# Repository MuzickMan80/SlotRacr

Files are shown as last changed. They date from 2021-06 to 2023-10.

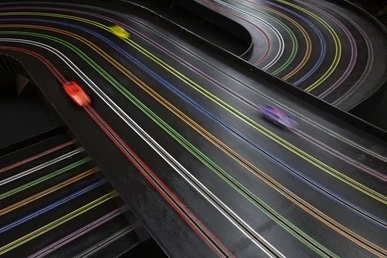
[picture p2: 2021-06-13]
frontend/assets/background.bmp

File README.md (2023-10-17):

Materials:
1 x HDMI Cable ($6) [https://www.adafruit.com/product/2775]
1 x Raspberry Pi 3 A+ ($25) [https://www.adafruit.com/product/4027]
1 x 5v 2.5a supply ($8) [https://www.adafruit.com/product/1995]
1 x 8GB SD Card
8 x Photo Transistor ($4) [https://www.adafruit.com/product/2831]
8 x 5.6kohm Resistor ($1)
8 x 1kohm Resistor ($1)

F to M jumper wires ($2) [https://www.adafruit.com/product/1954]
1 x Breadboard ($5) [https://www.adafruit.com/product/64]

1 x HDMI Display ($42) [https://www.amazon.com/Yasoca-Inch-Monitor-HDMI-Raspberry/dp/B089YSHMYS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]
Total: $93

Raspberry Pi setup:
1. Using Belena Etcher, burn Raspbian Lite OS image to the SD Card
1. Connect keyboard and monitor to Raspberry Pi, and let it startup
1. Login using username 'pi' and password 'raspberry'
1. Run 'sudo raspi-config' to enable WiFi and login to your network
  1. Select System Options->Wireless LAN and enter your SSID and password
  1. Select Interface Options->SSH to enable SSH access to your Raspberry Pi
1. Restart the Raspberry Pi to let it connect to your network
1. Run 
1. After it reboots, login again, and type the 'ifconfig' command to get the IP address for your network

From your computer:
1. Copy files to Raspbery Pi `./deploy.sh <pi ip>`

## References
https://disconnected.systems/blog/custom-rpi-image-with-github-travis/#travis
https://medium.com/platformer-blog/creating-a-custom-raspbian-os-image-for-production-3fcb43ff3630

## Ideas
Stop oog timer when red
Min 3 laps notice of low gas
Save race results
Online results database
Local sounds when low on gas

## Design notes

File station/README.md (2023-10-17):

# BOM Per Station
* $35 - Le Potato [https://www.amazon.com/dp/B0BDR2LWPC]
* $4  - 32gb microSD [https://www.amazon.com/dp/B07V1WC64X]
* $6  - USB Speaker [https://www.aliexpress.us/item/3256805016438808.html]
* $3  - USB Power Breakout [https://www.amazon.com/dp/B09W2QHL2P]
* $10 - RFID Card Reader [https://www.amazon.com/dp/B0B4BJK3W2]
* $3  - Ethernet Patch Cable [https://www.amazon.com/dp/B003EDZEDI]

Total Per Station: $61

# BOM Per Track
* $45 - 16 ports unmanaged switch 2x[https://www.amazon.com/dp/B07PFYM5MZ]
* $3  - Ethernet Patch Cable [https://www.amazon.com/dp/B003EDZEDI]
* $13 - USB Ethernet Adapter [https://www.amazon.com/dp/B00YUU3KC6]
* $10 - 30 Pack RFID Cards [https://www.amazon.com/gp/product/B07P8NCX55]

Total Per Track: $71
Total for 8 statsions: $498

# Le Potato Setup
1. Use Raspberry Pi Imager to burn Raspbian 11 lite to microSD cards [https://distro.libre.computer/ci/raspbian/11/2023-05-03-raspbian-bullseye-arm64%2Baml-s905x-cc.img.xz]
2. Enable SSH by creating empty file in boot partition called `ssh`
3. Set initial username and password by creating file called `userconf` containing username:encryptedpassword.  You can get the encrypted password via the command `openssl passwd -6`
4. Enable connection sharing to your Ethernet port on your development PC
5. Insert the microSD card into the Le Potato, connect an ethernet cable to your development PC, and power up the board.
6. Find the IP address of your Le Potato after it boots (this will take a little time, look for the green light to come on)
7. SSH into your Le Potato
8. Enable sound using `alsamixer`
  * Set volume (ACODEC) to 80
  * Set AIU ACODEC OUT EN to ON (Press M key)
  * Set AIU ACODEC SRC to I2S
9. Execute `sudo alsactl store` to persist settings

# Resources
[https://www.raspberrypi.com/documentation/computers/remote-access.html#setting-up-an-ssh-server]

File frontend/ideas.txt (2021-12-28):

Names (3 letters)
Seconds behind leader
Race Length
Save race data (for later replay)

Last Lap - White Flag

Final Lap - Checkerboard
  After finisher, everyone can finish last Lap

Flag if a racer is "missing"

New Leader

Race Report - 

Speaker - 
  When someone passes the leader
  When someone is gaining on the leader (over 5 laps)
  10 laps to go

Track disabling relays
Track slowing relays
Lane slowing relays
  Slow just one Lane

40 ohms on 13v ~ 6v  200mA @ 6v

12VA 600mA

Pit button
  When you push it, slows the Track
  If you push it too late, penalized
  When pass finish line, track shuts off
  If come in speeding, lose a Lap
  If speeding out of the pits, stop and go
  Lloyd Ruby 

Press Once to indicate they are going to pits
  Hold down at least 1.5 seconds before crossing finish line, slow 
  1.0 seconds - guaranteed speeding penalty

Need to tap within 2 seconds of crossing
  Resets after crossing finish

Status -
  Coming into pit = flashing yellow
  Slowing into pit = yellow
  Penalty = blue?
    Stop and go
  
Want 50, 100, 200 lap races
Typical race is 200 laps
  need to refuel every 45-48 laps

Time Trials mode - show current racer on top

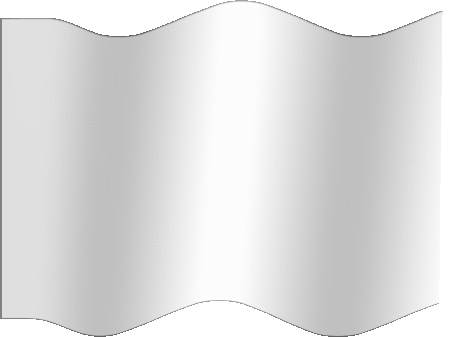
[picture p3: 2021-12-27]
frontend/assets/white-flag.gif

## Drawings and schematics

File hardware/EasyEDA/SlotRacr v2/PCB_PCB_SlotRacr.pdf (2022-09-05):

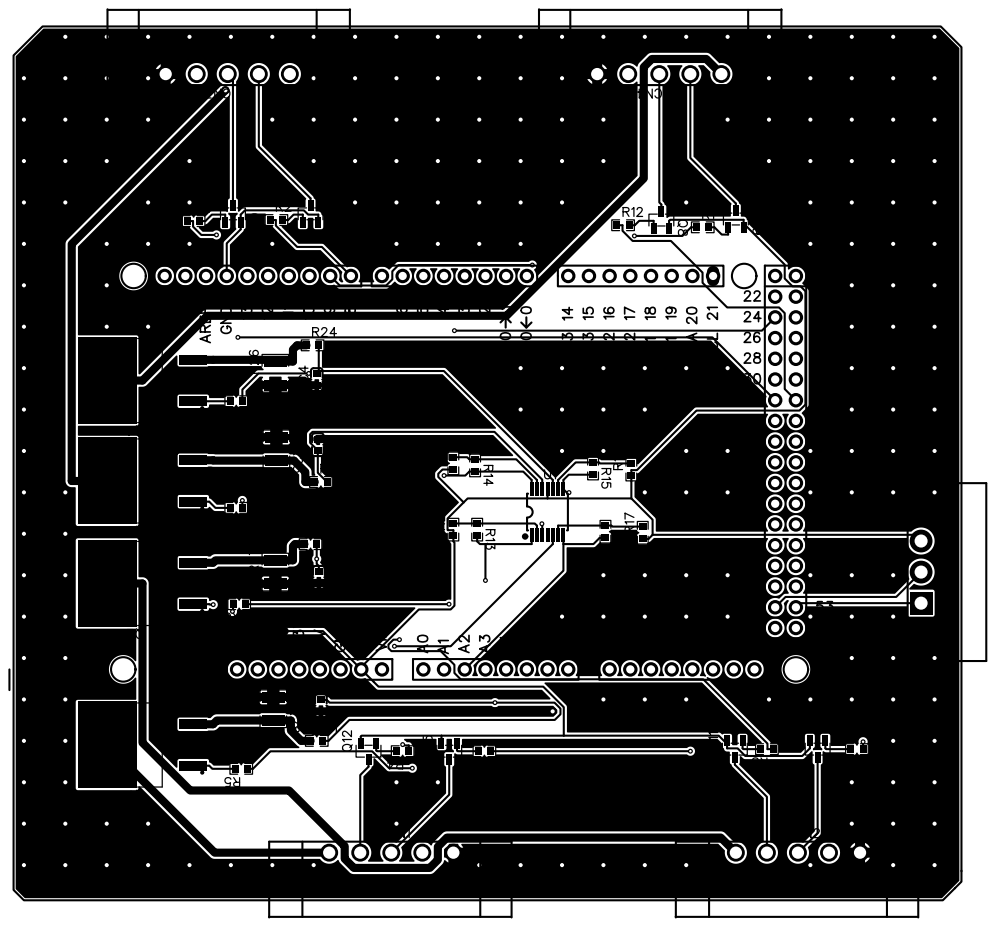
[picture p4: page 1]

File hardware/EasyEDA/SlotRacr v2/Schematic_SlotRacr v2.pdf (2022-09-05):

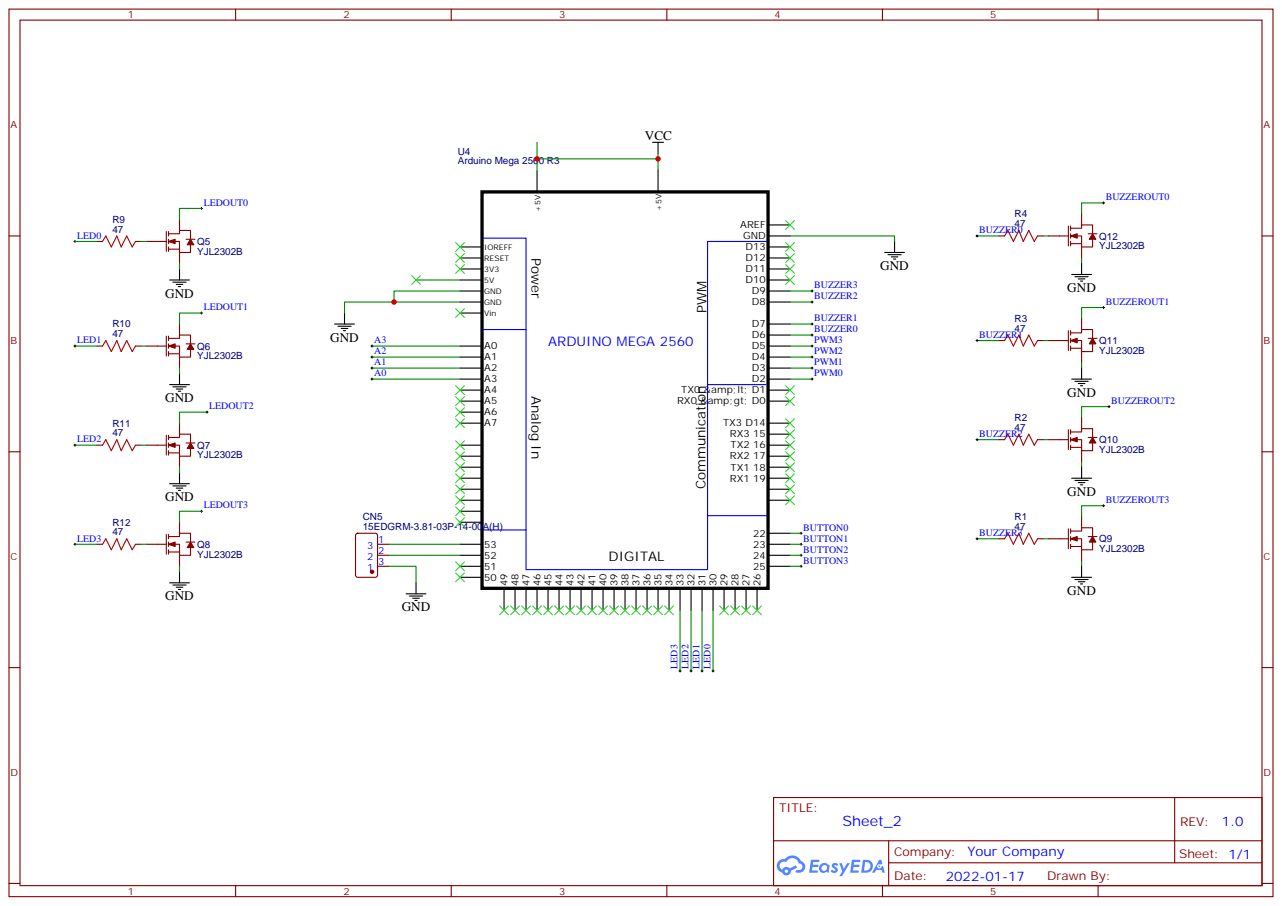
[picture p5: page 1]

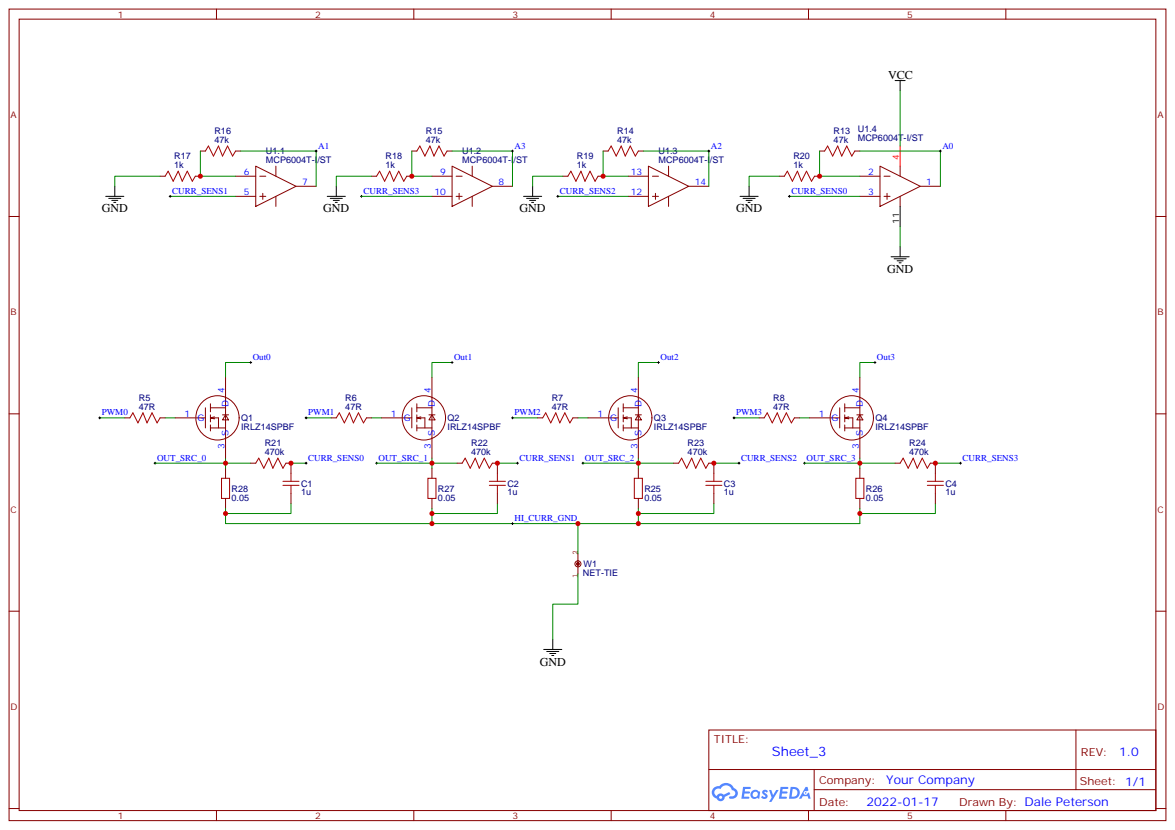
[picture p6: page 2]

Drawn By: Dale Peterson

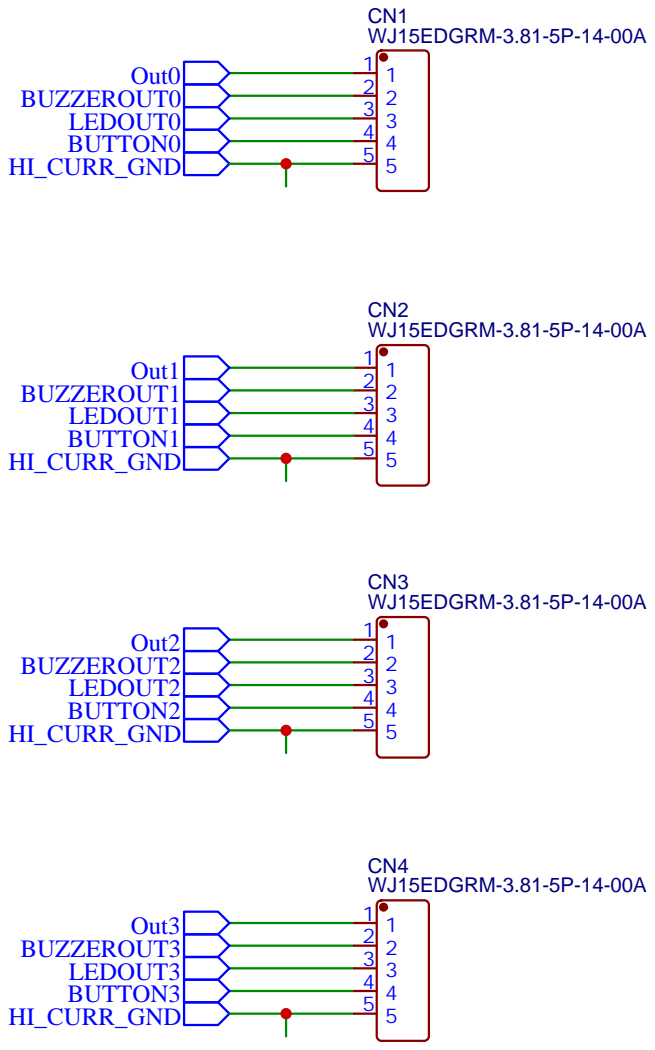
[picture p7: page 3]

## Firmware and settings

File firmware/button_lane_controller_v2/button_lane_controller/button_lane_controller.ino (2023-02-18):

/*
By default Arduino's analogWrite (and consequently pwmWrite() since it mimics analogWrite()) uses 8 bit 
pwm across all timers. 8 bit PWM allows for a total of 256 possible values. This library has some methods 
for fine tuning resolution if a higher resolution is needed:

void pwmWriteHR(uint8_t pin, uint16_t duty)
  Same a pwmWrite, except the range is 0 - 65535 (16 bit) instead 
  of 0 - 255 (8 bit)

float TimerX_GetResolution() (replace X with a timer number)
  Gets the timer's resolution in base 2. The value returned in other words 
  represents the number of bits required to represent the timer's range. ie 
  the value 7 means it takes 7 bits to represent all possible pin duties at 
  that frequency, or 7-bit resolution. Note that a float is returned, not 
  an int. 

float GetPinResolution(uint8_t pin)
  Returns the same value as TimerX_GetResolution(), but takes a pin number
  as a parameter so that the caller is timer agnostic.

There are several things to keep in mind when trying to optimize resolution:
 -pwmWriteHR() is only useful for 16 bit timers, since 8 bit timers are inherently limited to 8 bit pwm
 -The higher the frequency, the lower the resolution. pwmWriteHR() will automatically map input to the 
  actual timer resolution 
 -Resolution can be optimized in this way for 2 pins on the Uno (9 and 10), and 11 pins on the Mega (2, 
 3, 5, 6, 7, 8, 11, 12, 44, 45,  and 46)
  
Use the serial moniter to see output from this program
This example runs on mega and uno.
*/

#include <PWM.h>

#define countof(a) (sizeof(a)/sizeof(*a))

//use pin 11 on the mega for this example to work
int led = 13; // the pin that the LED is attached to

/*
timer 0 (controls pin 13, 4);
timer 1 (controls pin 12, 11);
timer 2 (controls pin 10, 9);
timer 3 (controls pin 5, 3, 2);
timer 4 (controls pin 8, 7, 6);
Next revision, we should try to put each one on it's own timer, and avoid timer 0 which
is used for 
*/
int trackPins[] = {
  2, 3, 4, 5
};

int currentSensePins[] = {
  A3, A2, A1, A0
};

int buttonPins[] = {
  22, 23, 24, 25, 52, 53
};

int lightPins[] = {
  30, 31, 32, 33
};

int buzzerPins[] = {
  6, 7, 8, 9
};

int controlButtonPins[] = {
  52, 53
};

void setup()
{
  InitTimers(); //initialize all timers except for 0, to save time keeping functions
  Serial.begin(500000);
  Serial.println();

  pinMode(led, OUTPUT);
  digitalWrite(led, HIGH);

  for (int i = 0; i < countof(lightPins); ++i)
  {
    pinMode(lightPins[i], OUTPUT);
  }
  for (int i = 0; i < countof(trackPins); ++i)
  {
    pinMode(trackPins[i], OUTPUT);
  }
  for (int i = 0; i < countof(buzzerPins); ++i)
  {
    pinMode(buzzerPins[i], OUTPUT);
  }
  for (int i = 0; i < countof(buttonPins); ++i)
  {
    pinMode(buttonPins[i], INPUT_PULLUP);
  }
}

const int numButtons = countof(buttonPins);
int buttonStates[numButtons] = {0};
int buttonDelays[numButtons] = {0};

unsigned long lastButtonCheck = 0;
unsigned long buttonTickMs = 5;
unsigned int buttonDebounceTicks = 10;
unsigned int ticksPerMs = 6;
int test = 0;

void updateButtonStates()
{
  for (int i = 0; i < numButtons; ++i)
  {
    int lastState = buttonStates[i];
    int state = digitalRead(buttonPins[i]);
    int buttonDelay = buttonDelays[i];

    if (state != lastState)
    {
      if (buttonDelay < buttonDebounceTicks)
      {
        buttonDelays[i]++;
      }
      else
      {        
        buttonStates[i] = state;
        buttonDelays[i] = 0;

        if(test) {
          writeOutputState(i,!state);
          writeOutputPower(i,state ? 0:60000);
          writeBuzzer(i,!state);
        }
      }
    }
    else
    {
      buttonDelays[i] = 0;
    }
  }
}

void pollButtons()
{
  if (lastButtonCheck++ > buttonTickMs*ticksPerMs)
  {
    lastButtonCheck = 0;
    updateButtonStates();
  }
}

void sendButtonStates()
{
  for (int i = 0; i < numButtons; ++i)
  {
    Serial.write(buttonStates[i] ? '0' : '1');
  }
  Serial.println();
}

bool writeOutputState(int output, int state)
{
  if (output < 0 || output >= countof(lightPins))
    return false;
  
  digitalWrite(lightPins[output], state ? HIGH : LOW);
  return true;
}

bool writeOutputPower(int output, uint16_t power)
{
  if (output < 0 || output >= countof(trackPins))
    return false;
  
  pwmWriteHR(trackPins[output], power);
  return true;
}

bool writeOutputFreq(int freq)
{
  for (int lane = 0; lane < countof(trackPins); ++lane)
  {
    writeOutputPower(lane, 0);
    SetPinFrequency(trackPins[lane], freq);
  }
  
  return true;
}

bool writeBuzzer(int output, int on)
{
  if (output < 0 || output >= countof(buzzerPins))
    return false;
  
  digitalWrite(buzzerPins[output],on?HIGH:LOW);  
  return true;
}

int lastTrackPowerLane = 0;
int trackPowers[countof(currentSensePins)] = {0};
 
void updateTrackPowers()
{
  int trackPower = analogRead(currentSensePins[lastTrackPowerLane]);
  trackPowers[lastTrackPowerLane] = (trackPowers[lastTrackPowerLane] * 9 + trackPower) / 10;
  
  lastTrackPowerLane = (lastTrackPowerLane+1) % countof(currentSensePins);
  
  if (test == 2 && trackPowers[lastTrackPowerLane] > 30) 
  {
    Serial.print(lastTrackPowerLane);
    Serial.write(" : ");
    sendTrackPower(lastTrackPowerLane);
  }
}

bool sendTrackPower(int lane)
{
  if (lane < 0 || lane >= countof(currentSensePins))
    return false;
  
  Serial.println(trackPowers[lane]);
  return true;
}

bool sendTrackPowers()
{
  for (int lane = 0; lane < countof(currentSensePins); ++lane)
  {
    sendTrackPower(lane);
  }
  return true;
}

struct OutOfGasState
{
  bool enabled;
  int onTick;
  int offTick;
  uint16_t onPower;
  uint16_t offPower;
};

OutOfGasState oogStates[countof(trackPins)] = {{false,0,0,0,0}};
int oogTick = 0;
int oogPeriodMs = 170;
int oogPeriodTicks = oogPeriodMs*ticksPerMs;
const long powerMax = 65536L;

bool setOutOfGasPeriod(int periodMs)
{
  if (periodMs < 10 || periodMs > 500) {
    return false;
  }
  
  oogPeriodMs = periodMs;
  oogPeriodTicks = oogPeriodMs * ticksPerMs;

  for (int lane = 0; lane < countof(trackPins); ++lane)
  {
    stopOutOfGas(lane);
  }

  return true;
}

// car type 1:
// 120ms, 15k, 50k, 15k
// car type 2:
// 200ms, 15k, 65k, 30k
// car type 1:
// 200ms, 15k, 65k, 13k
// 170ms, 23k, 50k, 0k
bool startOutOfGas(int lane, int32_t duty, int32_t onPower, int32_t offPower)
{
  if (lane < 0 || lane >= countof(trackPins))
    return false;

  if (duty < 0 || duty > powerMax)
    return false;
  if (onPower < 0 || onPower > powerMax)
    return false;
  if (offPower < 0 || offPower > powerMax)
    return false;

  int onTime = duty * oogPeriodTicks / powerMax;
  int onTick = lane * oogPeriodTicks / countof(trackPins);
  int offTick = (onTick + onTime) % oogPeriodTicks;

  oogStates[lane].onTick = onTick;
  oogStates[lane].offTick = offTick;
  oogStates[lane].onPower = onPower;
  oogStates[lane].offPower = offPower;
  oogStates[lane].enabled = onTick != offTick;

  int startPower = onPower;
  if (onTick == offTick) {
    startPower = onTime == 0 ? offPower : onPower;
    pwmWriteHR(trackPins[lane], startPower);
  }
  
  return true;
}

bool stopOutOfGas(int lane)
{
  if (lane < 0 || lane >= countof(trackPins))
    return false;
    
  oogStates[lane].onTick = 0;
  oogStates[lane].offTick = 0;
  oogStates[lane].enabled = false;  
}

void runOutOfGas()
{
  oogTick = (oogTick + 1) % oogPeriodTicks;

  for (int lane = 0; lane < countof(trackPins); ++lane)
  {
    if (oogStates[lane].enabled)
    {
      if (oogStates[lane].onTick == oogTick)
      {
        pwmWriteHR(trackPins[lane], oogStates[lane].onPower);
      }
      else if (oogStates[lane].offTick == oogTick)
      {
        pwmWriteHR(trackPins[lane], oogStates[lane].offPower);
      }
    }
  }  
}

void runCommand(char* cmd)
{
  int pinStates;
  int32_t outNum;
  int32_t outFreq;
  int32_t outPower;
  int32_t onPower;
  int32_t idlePower;
  int32_t outState;
  bool ok=true;
  switch(cmd[0]) {
    case 'r':
      sendButtonStates();
      break;
    case 'w':
      outNum = atol(strtok(cmd+1, ","));
      outState = atol(strtok(NULL, ","));
      ok=writeOutputState(outNum, outState);
      break;
    case 'o':
      outNum = atol(strtok(cmd+1, ","));
      outPower = atol(strtok(NULL, ","));
      ok=writeOutputPower(outNum, outPower);
      break;
    case 'f':
      outFreq = atol(strtok(NULL, ","));
      ok=writeOutputFreq(outFreq);
      break;
    case 'b':
      outNum = atol(strtok(cmd+1, ","));
      outFreq = atol(strtok(NULL, ","));
      ok=writeBuzzer(outNum, outFreq);
      break;
    case 't':
      outState = atol(strtok(cmd+1, ","));
      test = outState;
      break;
    case 'p':
      outNum = atol(strtok(cmd+1, ","));
      ok=sendTrackPower(outNum);
      break;  
    case 'q':
      ok=sendTrackPowers();
      break;
    case 'g':
      outNum = atol(strtok(cmd+1, ","));
      outPower = atol(strtok(NULL, ","));
      onPower = atol(strtok(NULL, ","));
      idlePower = atol(strtok(NULL, ","));
      ok=startOutOfGas(outNum, outPower, onPower, idlePower);
      break;
    case 's':
      outFreq = atol(strtok(cmd+1, ","));
      ok=setOutOfGasPeriod(outFreq);
      break;
    default:
      ok=0;
      break;
  }
  Serial.println(ok?"ok":"err");
  Serial.flush();
}

void processSerial()
{  
  const int maxInData = 30;
  static char inData[maxInData];
  static int inDataOffset = 0;
  static int toggle = LOW;
  
  if (Serial.available() > 0)
  {
    char received = Serial.read();
    inData[inDataOffset++] = received;

    if (received == '\n' || received == '\r' || inDataOffset == maxInData-1)
    {
      inData[inDataOffset] = 0;
      inDataOffset = 0;

      runCommand(inData);

      digitalWrite(led, toggle);
      toggle = !toggle;
    }
  }
}

unsigned long lastLoopTime = 0;
int loopsInSec = 0;

void displayCyclesPerSecond()
{
  if ((millis() - lastLoopTime) < 1000)
  {
    loopsInSec++;
  }
  else
  {
    Serial.println(loopsInSec);
    loopsInSec = 0;
    lastLoopTime = millis();
  }
}

void loop()
{
  pollButtons();
  updateTrackPowers();
  runOutOfGas();
  processSerial();

  if (test == 2)
  {
    displayCyclesPerSecond();
  }
}

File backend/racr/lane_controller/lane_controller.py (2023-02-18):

from __future__ import annotations
from typing import List
import serial
import asyncio
from .lane_power import LanePower
import logging

logger = logging.getLogger(__name__)
lane_logger = logging.getLogger('lane_power')

lane_mappings = [
    (1,0),
    (1,1),
    (1,2),
    (1,3),
    (0,0),
    (0,1),
    (0,2),
    (0,3)
]

class LaneController: # pragma: no cover
    def __init__(self):
        self.ports = []
        self.tasks = []
        self.button_handlers = []
        self.last_state = []
        self.lane_power = []
        self.target_lane_power = []

        for i in range(10):
            self.button_handlers.append(None)
            self.last_state.append(False)

        for i in range(8):
            self.lane_power.append(LanePower())
            self.target_lane_power.append(LanePower())

        try:
            self.ports.append(serial.Serial('/dev/ttyACM2', 500000, timeout=0.1))
            print("Opened serial port to lane controller 1")
            self.ports.append(serial.Serial('/dev/ttyACM0', 500000, timeout=0.1))
            print("Opened serial port to lane controller 2")
            self.start_polling()
            
            for i in range(8):
                try:
                    self.set_light(i,1)
                except:
                    pass
                try:
                    self.set_light(i,0)
                except:
                    pass

        except Exception as ex:
            print(f"Failed to open serial port: {ex}")

    def start_polling(self):
        loop = asyncio.get_event_loop()
        if self.ports[0]:
            self.tasks.append(loop.create_task(self.poll_loop()))
        if self.ports[1]:
            self.tasks.append(loop.create_task(self.poll_loop()))

    def get_lane(self,port,pin):
        for lane in range(8):
            lane_map = lane_mappings[lane]
            if lane_map[0] == port and lane_map[1] == pin:
                return lane
        return -1

    def get_button(self,port,idx):
        if port == 0 and idx == 4:
            return 8
        if port == 0 and idx == 5:
            return 9
        for lane in range(8):
            lane_map = lane_mappings[lane]
            if lane_map[0] == port and lane_map[1] == idx:
                return lane
        return -1

    async def poll_loop(self):
        while True:
            for lane in range(8):
                try:
                    if self.lane_power[lane] != self.target_lane_power[lane]:
                        self.lane_power[lane].nudge(self.target_lane_power[lane])
                        self.send_lane_power(lane)
                except Exception as err:
                    print(f'Error nudging lane power {lane}: {err}')

            for port in range(2):
                try:
                    response = self.send_command(port,'r')
                    button=0
                    for char in response:
                        if button >= 8:
                            break
                        button_state = char == '1'
                        lane = self.get_button(port, button) 
                        if lane != -1:
                            if button_state != self.last_state[lane]:
                                await self.handle_button(lane, button_state)
                                self.last_state[lane] = button_state
                        button = button + 1
                except Exception as err:
                    print(f'Error occurred reading buttons from {port}: {err}')

            await asyncio.sleep(.01)

    async def handle_button(self, lane, state):
        handler = self.button_handlers[lane]
        if lane < 8:
            self.set_light(lane, state)
        if handler:
            await handler(state)

    def send_command(self, port, command):
        response = None
        serport = self.ports[port]
        serport.reset_input_buffer()
        serport.writelines([command.encode(), b'\r'])
        logger.debug('command[%d]: %s', port, command)
        while True:
            line = serport.readline().decode()
            logger.debug('response: %s', line)
            if line == "ok\r\n":
                break
            elif line == "err\r\n":
                raise Exception("Error sending command")
            elif line == "\r\n":
                break
            else:
                response = line
        return response

    def monitor_button(self, button, handler):
        self.button_handlers[button] = handler

    def set_frequency(self, freq=100):
        self.send_command(0,f'f{freq}')
        self.send_command(1,f'f{freq}')

    def set_oog_freq(self, freq=6):
        period=round(1000/freq)
        self.send_command(0,f's{period}')
        self.send_command(1,f's{period}')

    def set_oog(self, lane, percent, onPercent, offPercent, immediate: bool = False):
        self.target_lane_power[lane].powerPercent = percent
        self.target_lane_power[lane].onDutyPercent = onPercent
        self.target_lane_power[lane].offDutyPercent = offPercent
        if immediate:
            self.lane_power[lane].powerPercent = percent
            self.lane_power[lane].onDutyPercent = onPercent
            self.lane_power[lane].offDutyPercent = offPercent
            self.send_lane_power(lane)

    def send_lane_power(self, lane):
        try:
            lane_map = lane_mappings[lane]
            lane_power: LanePower = self.lane_power[lane]
            on_time = int(65535*(lane_power.powerPercent/100))
            on_pwr = int(65535*(lane_power.onDutyPercent/100))
            off_pwr = int(65535*(lane_power.offDutyPercent/100))
            lane_logger.info('%d - %d,%d,%d', lane, on_time, on_pwr, off_pwr)
            self.send_command(lane_map[0],f'g{lane_map[1]},{on_time},{on_pwr},{off_pwr}')  
        except Exception as err:
            print(f'Error setting lane speed: {err}')  

    def set_light(self, light, on):
        lane_map = lane_mappings[light]
        on_val = 0
        if on:
            on_val = 1
        self.send_command(lane_map[0],f'w{lane_map[1]},{on_val}')

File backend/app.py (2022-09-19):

#!/usr/bin/env python3

import asyncio
from app_server import TrackManagerApp
import argparse

parser = argparse.ArgumentParser()
parser.add_argument('--target_ip', help='IP Address of the pigpio service', default=None)
parser.add_argument('--mock', help='Mock IO backend', action='store_true')

args = parser.parse_args()

if __name__ == '__main__':
    loop = asyncio.get_event_loop()

    if not args.mock:
        from racr.io.pi_io_manager import PiIoManager
        app = TrackManagerApp(PiIoManager(loop,args.target_ip))
    else:
        from racr.io.fake_io_manager import FakeIoManager
        app = TrackManagerApp(FakeIoManager(loop))

    async def run_app():
        await app.start()
        while True:
            await asyncio.sleep(3600)

    loop.run_until_complete(run_app())
    

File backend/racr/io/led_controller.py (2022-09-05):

import serial

class LedController: # pragma: no cover
    def __init__(self):
        self.port = None
        try:
            self.port = serial.Serial('/dev/ttyACM1', 500000, timeout=0.1)
            print("Opened serial port to led controller")
            
            for i in range(3):
                try:
                    self.set_light(i,1)
                except:
                    pass
                try:
                    self.set_light(i,0)
                except:
                    pass

        except Exception as ex:
            print(f"Failed to open serial port: {ex}")

    def set_light(self, light, on):
        on_val = 1 if on else 0
        self.send_command(f'w{light},{on_val}')
        
    def send_command(self, command):
        if not self.port:
            return

        response = None
        serport = self.port
        serport.reset_input_buffer()
        serport.writelines([command.encode(), b'\r'])
        # print(f'command: "{command}"')
        while True:
            line = serport.readline().decode()
            # print(f'response: "{line}"')
            if line == "ok\r\n":
                break
            elif line == "err\r\n":
                raise Exception("Error sending command")
            elif line == "\r\n":
                break
            else:
                response = line
        return response

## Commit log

2021-12-12 Run timer_update after network online
2021-12-12 Add timer_update to wants
2021-12-12 Enable pullup on reset button
2021-12-27 Reorganize backend
    [lane_controller.kicad_pcb, lane_controller.sch, slot_race_timer.dsn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]
2021-12-27 Show driver info
2021-12-27 Show SDL driver name
2021-12-28 Fix compatibility with 3.7
    [app.py]
2021-12-28 Refactor track manager
2021-12-29 Move pin assignments into io managers
2021-12-29 temporarily disable reset button
2021-12-29 Fix pit pin
2022-01-09 Commit lane controller board
    [MEGA2560_Rev3e.brd, MEGA2560_Rev3e.sch, lane_controller.kicad_pcb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]
2022-01-10 Fix root web access
    [app_rest_api.py]
2022-01-10 Attempt to fix settings saving
    [app_server.py]
2022-01-16 switch to 5
2022-01-16 throttle when in penalty
2022-01-31 commit hardware
    [lane_controller.kicad_pcb, lane_terminal_block.kicad_pcb, lane_terminal_block.sch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]
2022-02-03 Fix settings rest API
    [app_rest_api.py, app_server.py, track_manager.py]
2022-02-12 Commit arduino source
2022-02-12 Fix web frontend after moving working directory
    [app_rest_api.py]
2022-02-13 Fix startup issue if lane_controller can't be connected
    [lane_controller.py]
2022-02-13 Catch error when starting
    [lane_controller.py]
2022-02-13 Add track simulator setting
2022-02-13 Remove throttle column from frontend
2022-02-13 Ensure settings are restored and saved as correct type
    [app_server.py]
2022-02-14 Cleanup lane indexing issues
    [fake_io_manager.py, io_manager.py, pi_io_manager.py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]
2022-02-19 Use current tick on pit button
2022-02-19 Pit button debugging
2022-09-05 Checkin hardware files
    [MEGA2560_Rev3e.brd, MEGA2560_Rev3e.sch, lane_controller.kicad_pcb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]
2022-09-07 Add text font for driver and status
2022-09-11 Swap hardcoded lane controller
    [lane_controller.py]
2022-09-23 Fix a few things (hopefully)
    [lane_controller.py]
2022-09-23 Fix state buttons
2022-09-23 Ramp up lane power
2023-02-18 add lane power logger
2023-02-18 disable socketio logger
2023-02-18 Stop immediately, fix burst on track power change
    [button_lane_controller.ino, lane_controller.py]
2023-10-17 Add station registration
    [Sound 02 Pit stops.xlsx, Sound 03 Pit stops.xlsx, Sound 04 Pit stops.xlsx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]
2023-10-22 Update attached stations
2023-10-22 Switch to ogg files, parse station update
2023-11-04 Add race sounds
    [Sound 02 Pit stops.xlsx, Sound 03 Pit stops.xlsx, Sound 04 Pit stops.xlsx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]
2023-11-04 Delay one track by 1 second
2023-11-04 Add track reset to web frontend
2023-11-04 Move button
